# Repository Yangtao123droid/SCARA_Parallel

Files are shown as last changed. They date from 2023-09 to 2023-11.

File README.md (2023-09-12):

【SCARA_Parallel】
=

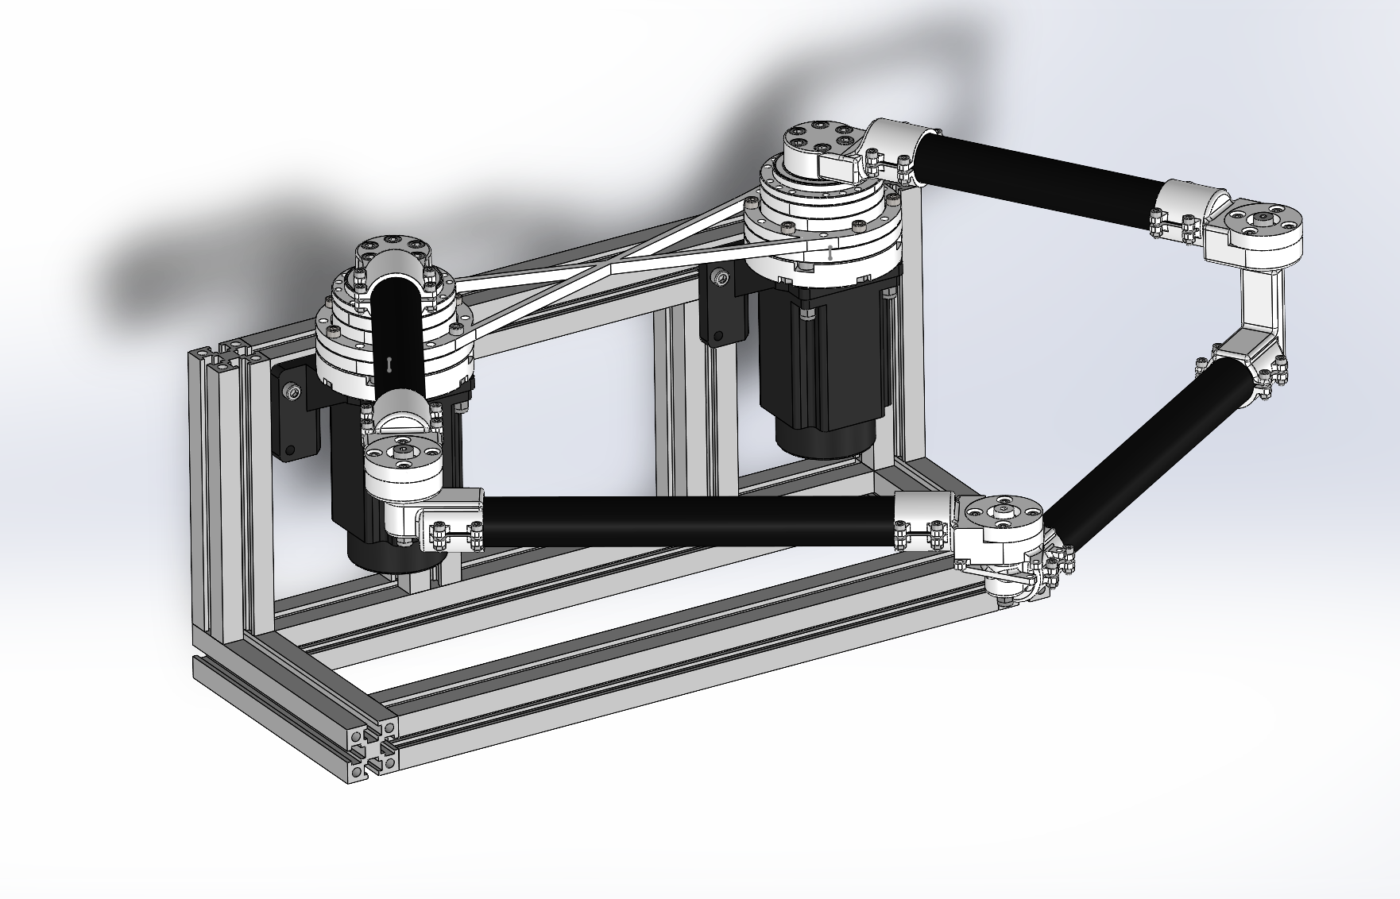
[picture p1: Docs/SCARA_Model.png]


毕设设计的一款并联SCARA机械臂，闭环步进电机，谐波减速，碳纤维杆件，3D打印关节，运动控制，直线插补
=
后面会慢慢更新MATLAB运动学仿真、基于STM32F407的运动控制代码、插补代码以及一些思路分享等等
    
更新说明
=
2023.9.11 更新3D模型 ---所有的零件、电机、减速器、杆件、机加工轴、3D打印关节、装配体文件等等

1、硬件选型与结构设计
=
1.1、电机的选择  
=
电机因为成本考虑问题和项目工作量问题，没有选择使用伺服电机或者无刷电机作为驱动关节，而是选用的
    
闭环步进电机电机的型号是杰美康的57J1880，在闲鱼上淘的,加驱动器一套大概150元，驱动器的型号是2HSS57，

也是杰美康的闭环驱动器，里面自带了电机控制算法，有电流环位置环等等，控制起来和普通的步进电机驱动器  

一样，发脉冲就好了。

后面有时间也许会考虑做一个无刷电机作为关机的版本，FOC控制，可以加入动力学的控制

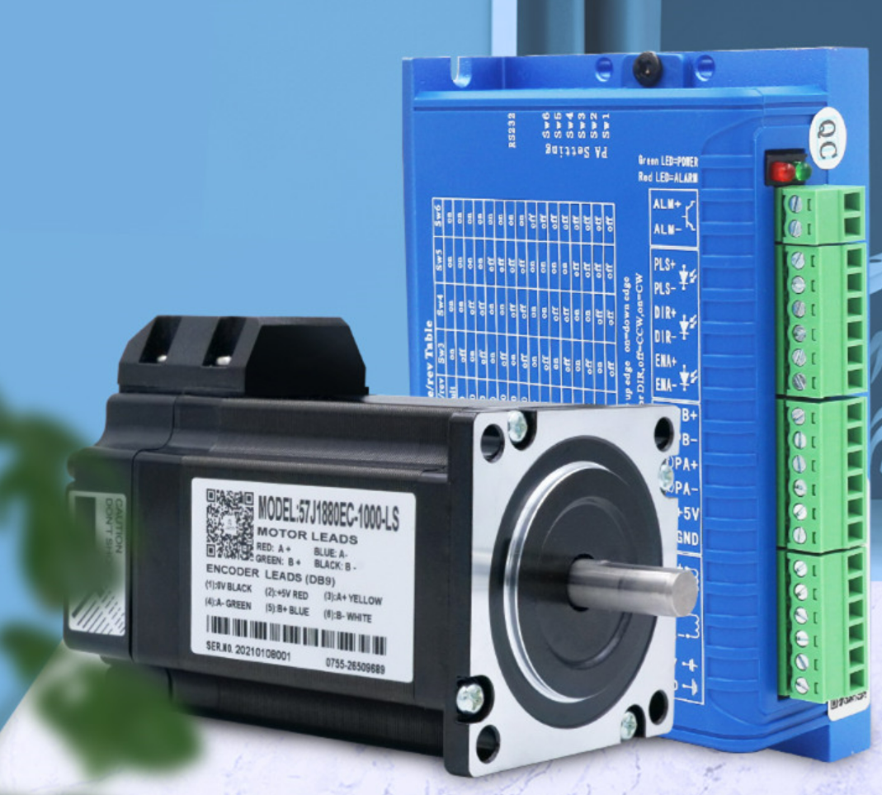
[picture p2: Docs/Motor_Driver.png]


1.2、减速器
=
减速器选用的谐波减速，在闲鱼上淘的leaderdrive绿的谐波的LSCG系列减速器，17-50，减速比50，450元一个，减速器与电机出轴的

尺寸不一样，当时这里自己画了一个连轴器，相当于把电机轴加粗然后插进减速器的孔里面，用键销固定，再上顶丝，电机端

本来就是D型轴，直接卡住就好了，发的模型里面都可以找到零件和装配方法。


1.3、 关节旋转轴
=
这里当时是最苦恼的部分，因为不是机械方面专业的，所以自己完全不知道怎么去设计这部分旋转的关节，后面直接找到了这种

带法兰座的轴承，这样设计起来就容易很多了。
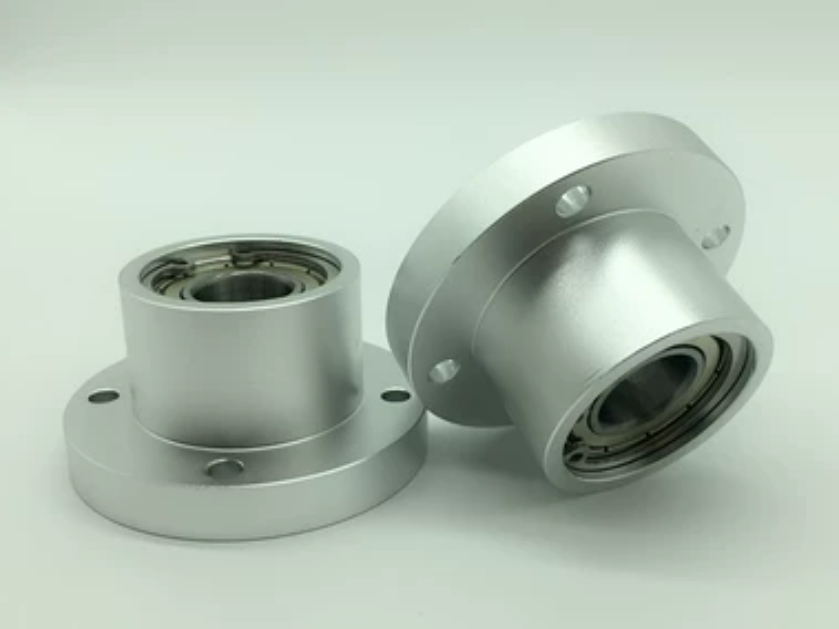
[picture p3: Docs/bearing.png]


1.4、 杆件的选择
=
当时也走了不少弯路，中间有一次甚至直接整个结构都用光固化打印的材料去搭，结果刚度完全不够，搭上去

整个结构就一点一点的塌下去了，后面还是换回了碳纤维管的方案。下面是用过的杆件，整整一箱



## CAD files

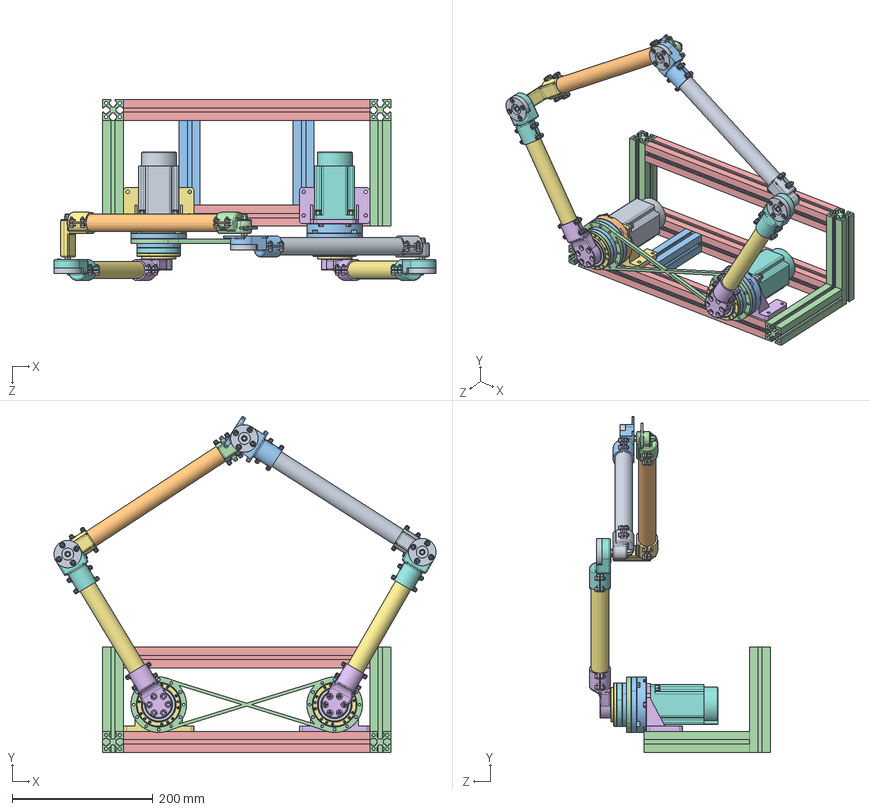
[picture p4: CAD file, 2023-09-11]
Solidworks_Model/SCARA.SLDASM
542.8 x 477.5 x 257.3 mm
闭环步进电机1
闭环步进电机2
电机支架1
电机支架2
减速器固定法兰1
减速器固定法兰2
横350mm x 3
竖150mm x 4
竖120mm x 2
M5锁紧螺母 x 17
RZC-17G______+____^________RZC-17G_LCSG-17-XXX-C-I(2)_LCSG-17-XXX-C-I x 2
RZC-17______^________RZC-17G_LCSG-17-XXX-C-I(2)_LCSG-17-XXX-C-I x 2
LHS-17-XXX-P03-I^LCSG-17-XXX-C-I(2)_LCSG-17-XXX-C-I x 2
DB-17-I^LCSG-17-XXX-C-I(2)_LCSG-17-XXX-C-I x 2
_ISO 7046-1 - M2 x 4 - Z --- 4N^LCSG-17-XXX-C-I(2)_LCSG-17-XXX-C-I x 8
LCS-17-XXX-P01^LCSG-17-XXX-C-I(2)_LCSG-17-XXX-C-I x 2
LCSG-17-P02^LCSG-17-XXX-C-I(2)_LCSG-17-XXX-C-I x 2
LCS-17-P05^LCSG-17-XXX-C-I(2)_LCSG-17-XXX-C-I x 2
________________M5 x 16_________________M5 x 16^LCSG-17-XXX-C-I(2)_LCSG-17-XXX-C-I x 12
LCS-17-P04-3^LCSG-17-XXX-C-I(2)_LCSG-17-XXX-C-I x 2
LCS-17-P04-1^LCSG-17-XXX-C-I(2)_LCSG-17-XXX-C-I x 2
LCS-17-P04-2^LCSG-17-XXX-C-I(2)_LCSG-17-XXX-C-I x 2
15Z-38475^LCSG-17-XXX-C-I(2)_LCSG-17-XXX-C-I x 2
电机轴加粗 x 2
键槽销 x 2
电机距离250mm确认
M4六角螺母 x 12
减速器连接关节 x 2
碳管_185mm x 2
中间关节_上 x 2
轴承 x 3
垫片 x 3
M3X14_固定轴承_中间关节 x 12
M3六角螺母 x 44
M3X12_锁紧碳管 x 32
M5六角螺母 x 3
M5铜柱18mm x 2
中间关节_下_长
M5铜柱50mm
中间关节_下
碳管_270mm
碳管_255mm
末端关节_上
末端关节_下

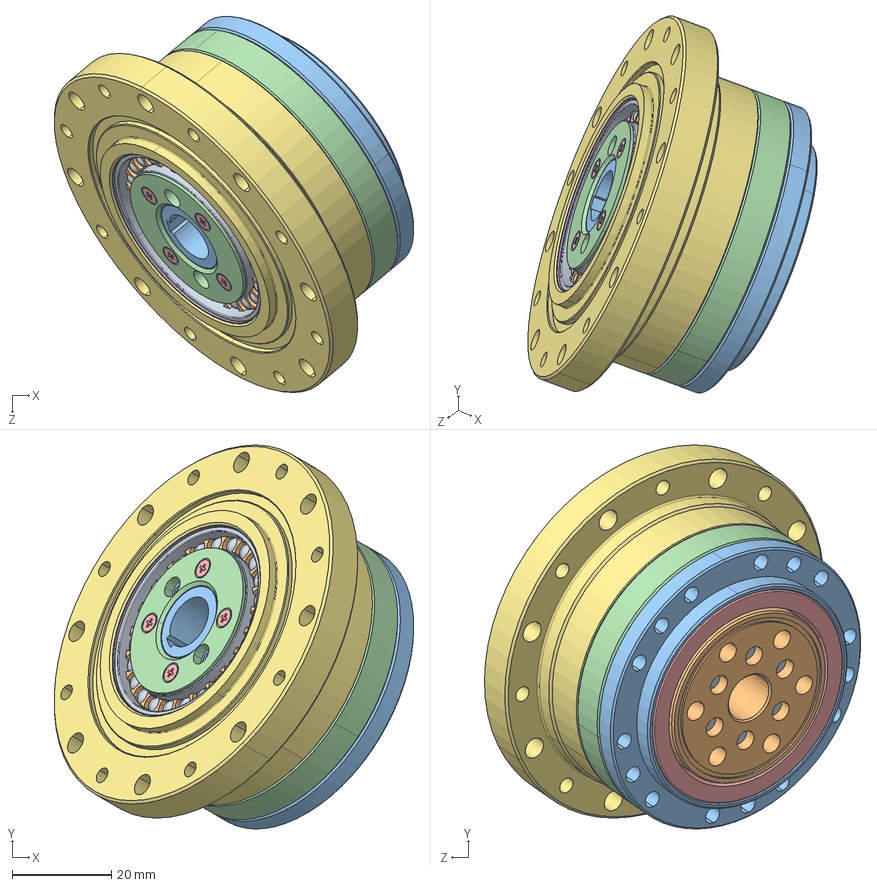
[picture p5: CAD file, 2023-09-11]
Solidworks_Model/减速器/谐波减速.SLDASM
72.3 x 77.3 x 75.7 mm
RZC-17G______+____^________RZC-17G_LCSG-17-XXX-C-I(2)_LCSG-17-XXX-C-I
RZC-17______^________RZC-17G_LCSG-17-XXX-C-I(2)_LCSG-17-XXX-C-I
LHS-17-XXX-P03-I^LCSG-17-XXX-C-I(2)_LCSG-17-XXX-C-I
DB-17-I^LCSG-17-XXX-C-I(2)_LCSG-17-XXX-C-I
_ISO 7046-1 - M2 x 4 - Z --- 4N^LCSG-17-XXX-C-I(2)_LCSG-17-XXX-C-I x 4
LCS-17-XXX-P01^LCSG-17-XXX-C-I(2)_LCSG-17-XXX-C-I
LCSG-17-P02^LCSG-17-XXX-C-I(2)_LCSG-17-XXX-C-I
LCS-17-P05^LCSG-17-XXX-C-I(2)_LCSG-17-XXX-C-I
________________M5 x 16_________________M5 x 16^LCSG-17-XXX-C-I(2)_LCSG-17-XXX-C-I x 6
LCS-17-P04-3^LCSG-17-XXX-C-I(2)_LCSG-17-XXX-C-I
LCS-17-P04-1^LCSG-17-XXX-C-I(2)_LCSG-17-XXX-C-I
LCS-17-P04-2^LCSG-17-XXX-C-I(2)_LCSG-17-XXX-C-I
15Z-38475^LCSG-17-XXX-C-I(2)_LCSG-17-XXX-C-I

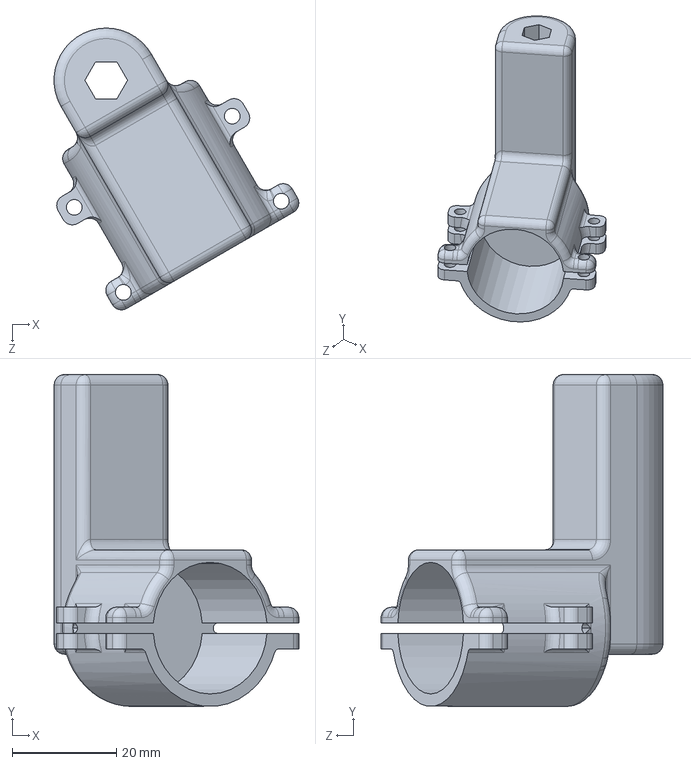
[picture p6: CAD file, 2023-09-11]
Solidworks_Model/打印件/中间关节_下_长.SLDPRT
46.9 x 63.5 x 54.0 mm

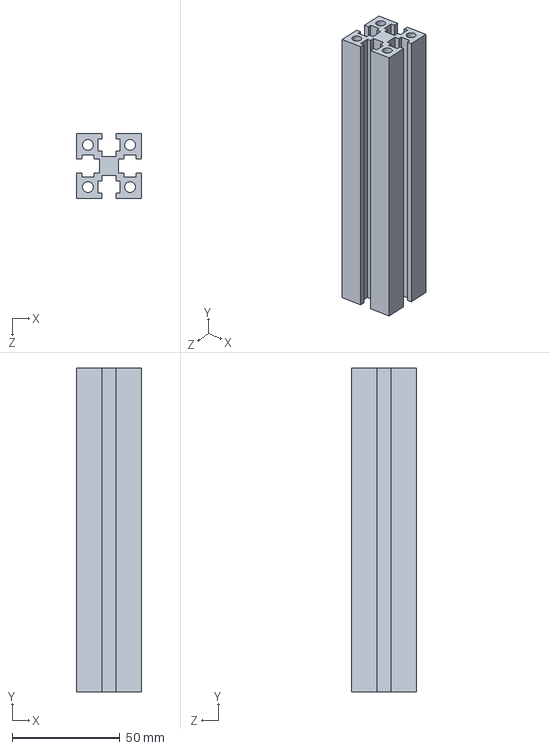
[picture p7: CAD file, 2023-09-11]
Solidworks_Model/机械臂固定底座/竖150mm.SLDPRT
30.0 x 150.0 x 30.0 mm

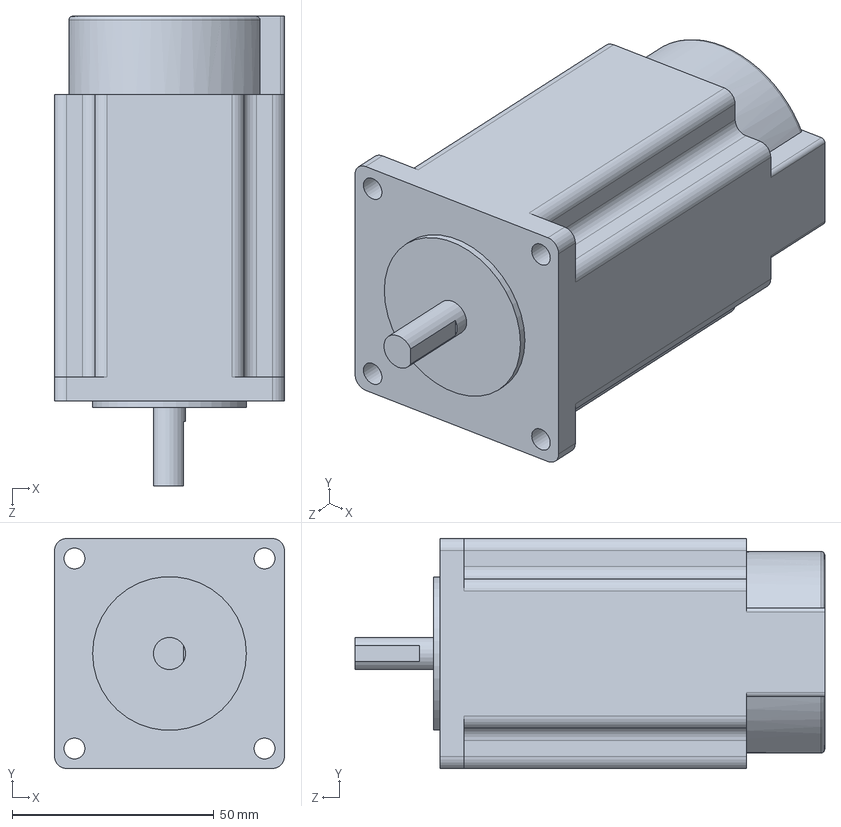
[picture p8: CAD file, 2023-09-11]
Solidworks_Model/电机_支架/闭环步进电机2.SLDPRT
57.0 x 57.0 x 116.4 mm

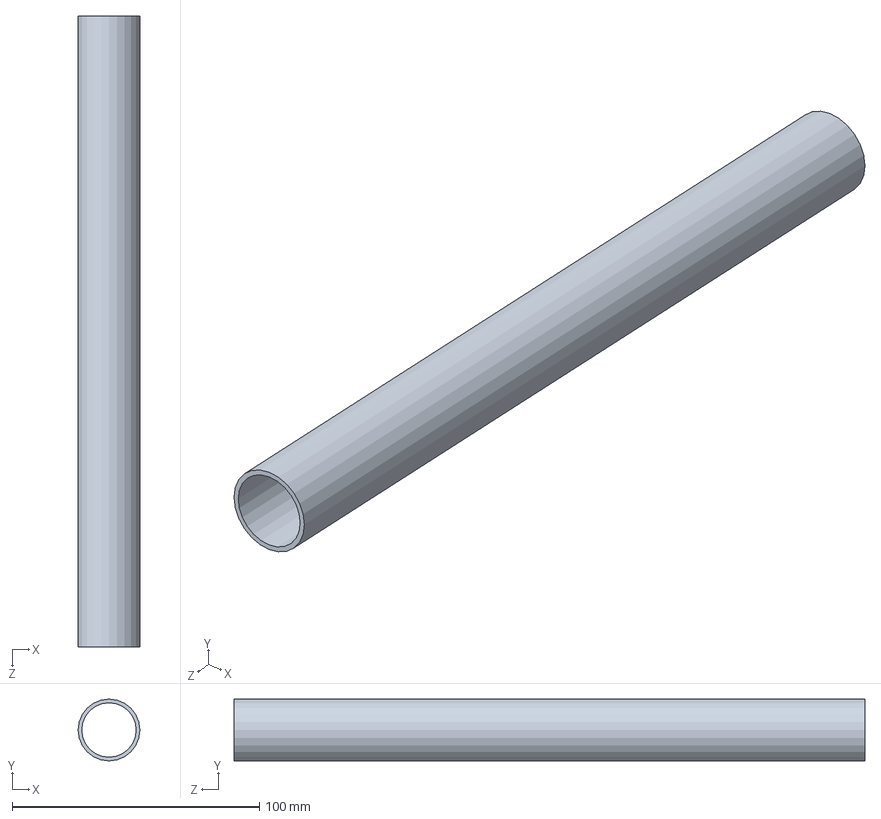
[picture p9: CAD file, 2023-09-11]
Solidworks_Model/碳纤维管/碳管_255mm.SLDPRT
25.0 x 25.0 x 255.0 mm

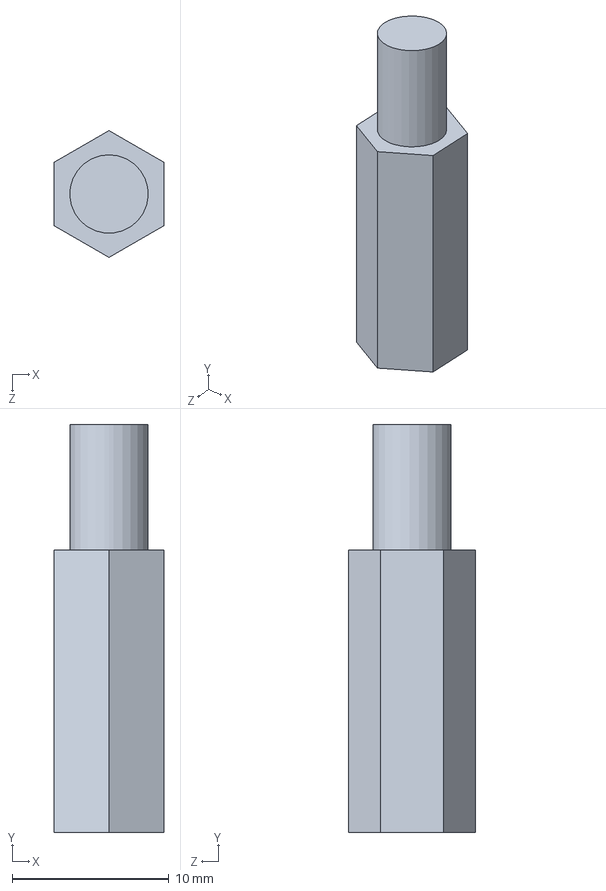
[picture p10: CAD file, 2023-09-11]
Solidworks_Model/螺丝_螺母_垫片_铜柱/M5铜柱18mm.SLDPRT
7.00 x 26.0 x 8.08 mm

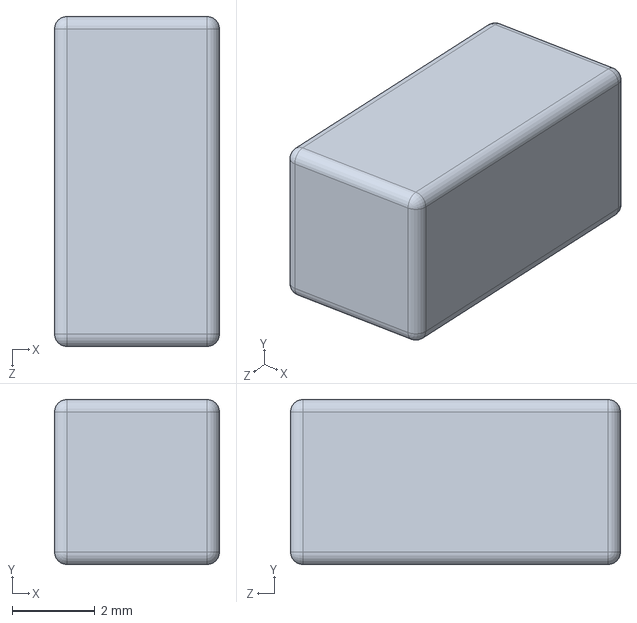
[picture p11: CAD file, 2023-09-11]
Solidworks_Model/轴加工_键槽销/键槽销.SLDPRT
4.00 x 4.00 x 8.00 mm

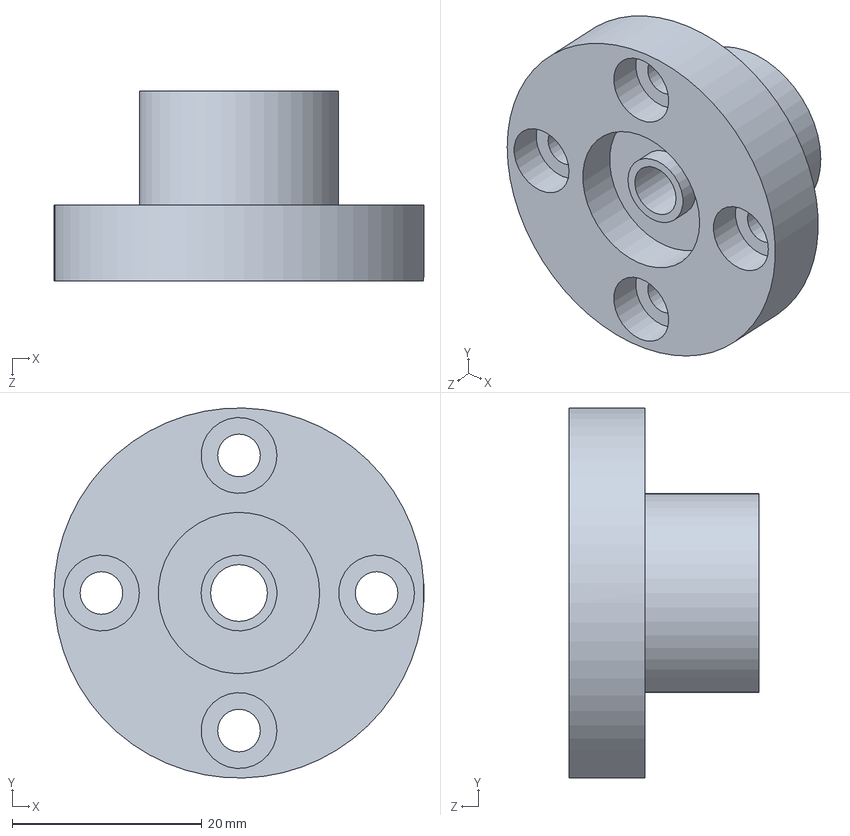
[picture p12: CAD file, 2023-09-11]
Solidworks_Model/轴承/轴承.SLDPRT
39.0 x 39.0 x 20.0 mm

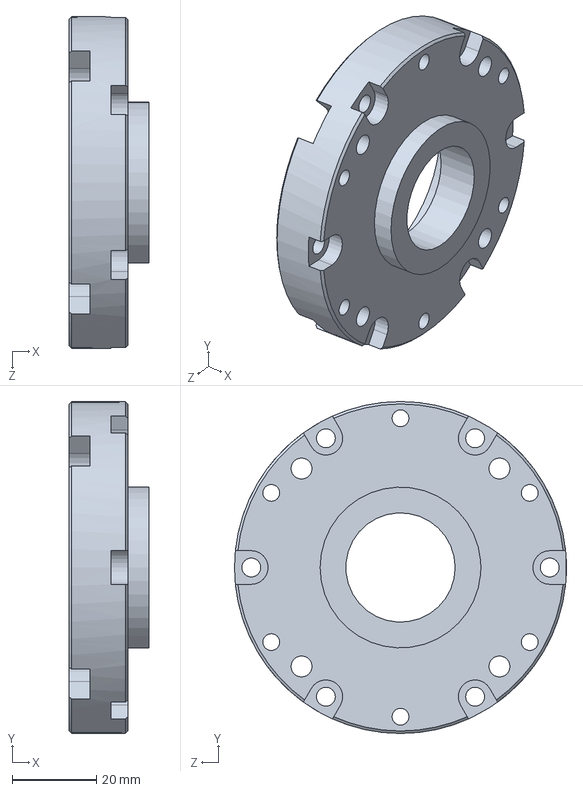
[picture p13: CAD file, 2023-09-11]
Solidworks_Model/打印件/减速器固定法兰2.SLDPRT
19.0 x 79.0 x 79.0 mm

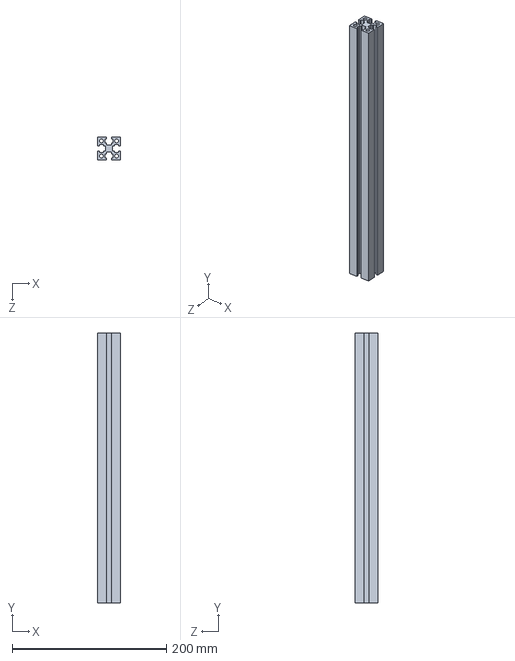
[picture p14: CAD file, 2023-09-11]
Solidworks_Model/机械臂固定底座/横350mm.SLDPRT
30.0 x 350.0 x 30.0 mm

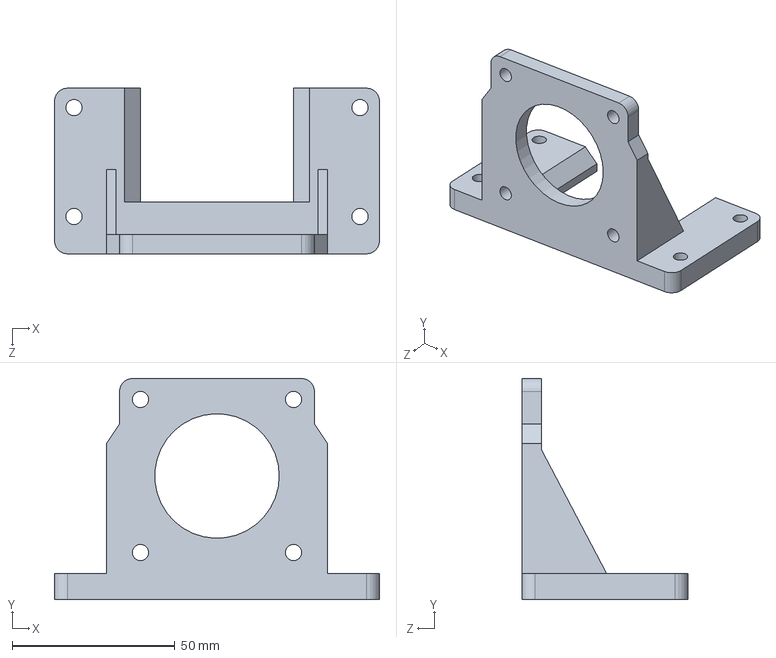
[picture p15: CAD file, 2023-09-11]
Solidworks_Model/电机_支架/电机支架2.SLDPRT
100.0 x 68.0 x 51.0 mm

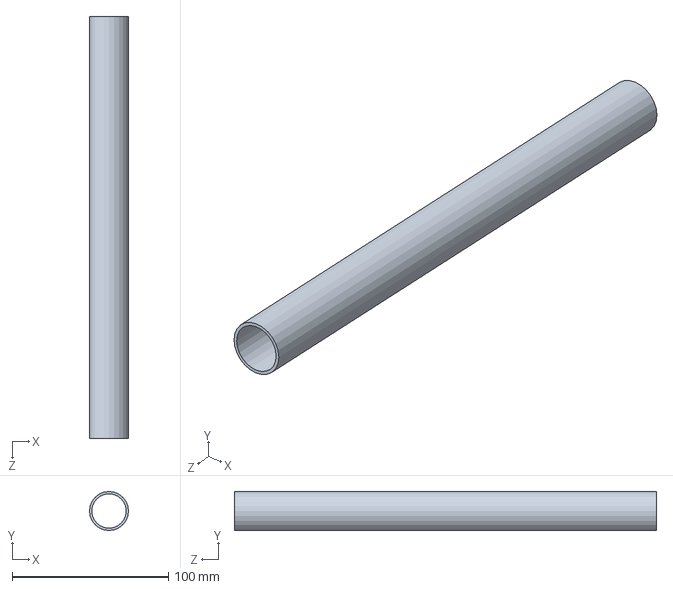
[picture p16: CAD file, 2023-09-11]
Solidworks_Model/碳纤维管/碳管_270mm.SLDPRT
25.0 x 25.0 x 270.0 mm

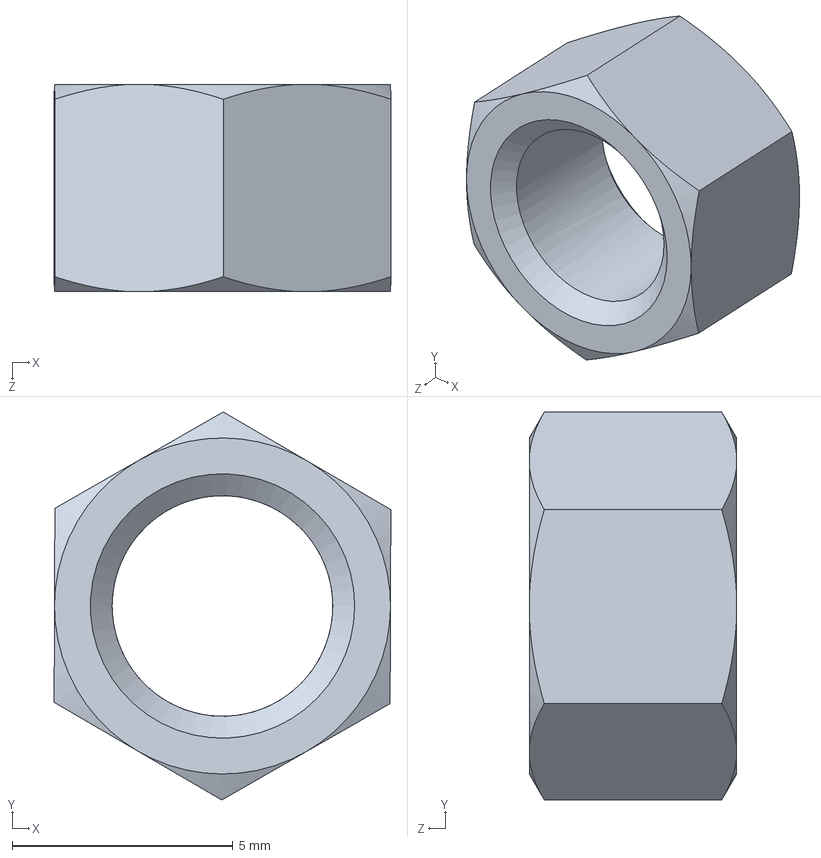
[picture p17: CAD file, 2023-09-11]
Solidworks_Model/螺丝_螺母_垫片_铜柱/M5六角螺母.SLDPRT
7.63 x 8.79 x 4.70 mm

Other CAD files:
Solidworks_Model/轴加工_键槽销/电机轴加粗.SLDPRT
Solidworks_Model/打印件/减速器固定法兰1.SLDPRT
Solidworks_Model/机械臂固定底座/竖120mm.SLDPRT
Solidworks_Model/电机_支架/电机支架1.SLDPRT
Solidworks_Model/打印件/中间关节_上.SLDPRT
Solidworks_Model/打印件/中间关节_下.SLDPRT
Solidworks_Model/打印件/减速器连接关节.SLDPRT
Solidworks_Model/打印件/末端关节_上.SLDPRT
Solidworks_Model/打印件/末端关节_下.SLDPRT
Solidworks_Model/打印件/电机距离250mm确认.SLDPRT
Solidworks_Model/碳纤维管/碳管_185mm.SLDPRT
Solidworks_Model/螺丝_螺母_垫片_铜柱/M3X12_锁紧碳管.SLDPRT
Solidworks_Model/螺丝_螺母_垫片_铜柱/M3X14_固定轴承_中间关节.SLDPRT
Solidworks_Model/螺丝_螺母_垫片_铜柱/M3六角螺母.SLDPRT
Solidworks_Model/螺丝_螺母_垫片_铜柱/M4×25_固定减速器_减速器法兰_电机距离确定打印件.SLDPRT
Solidworks_Model/螺丝_螺母_垫片_铜柱/M4六角螺母.SLDPRT
Solidworks_Model/螺丝_螺母_垫片_铜柱/M5×14_固定电机底座_机械臂底座.SLDPRT
Solidworks_Model/螺丝_螺母_垫片_铜柱/M5×25_固定关节_减速器.SLDPRT
Solidworks_Model/螺丝_螺母_垫片_铜柱/M5×25_固定电机_电机底座_减速器法兰.SLDPRT
Solidworks_Model/螺丝_螺母_垫片_铜柱/M5轴肩螺丝.SLDPRT
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

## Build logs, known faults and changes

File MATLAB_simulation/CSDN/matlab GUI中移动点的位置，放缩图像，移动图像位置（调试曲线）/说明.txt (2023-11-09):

1、进入界面，首先点击初始化按钮，会根据xData和YData数据进行画图（分别是x轴和y轴）

2、启动放缩和关闭放缩可以放缩图像

3、右移和左移图像可以移动坐标轴

4、保存数据按钮可以保存数据，x和y轴数据存在newX和newY数据

5、如果想要移动坐标轴，点击关闭放缩按钮，当鼠标停在数据点上时，按下鼠标左键拖动数据点即可移动数据，（注意，数据点不能是第一个和最后的数据点，且不会超过相邻数据点的范围）

6、另外，xData和yData不用逗号分隔数据，不要修改文件格式

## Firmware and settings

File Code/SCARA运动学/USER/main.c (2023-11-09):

#include "stm32f4xx.h"
#include "delay.h"
#include "led.h"
#include "key.h"
#include "pwm.h"
#include "motor.h" 
#include "SCARA.h"
#include "xbox.h"
#include "openmv.h"
#include "balance.h"

u16 pwmval=0;     
u16 ar1=5000;
u16 ar2=5000;
u16 ar3=5000;
u16 L1=1;
u16 L3=1;
u8 model_S = 0;
u8 key_up1 = 0;
u8 key_up2 = 0;
u8 key_up3 = 0;
u8 key_up4 = 0;
u8 model_pen = 0;

float XNN = 382.3376;


int main(void)
{
	NVIC_PriorityGroupConfig(NVIC_PriorityGroup_2);//设置系统中断优先级分组2
	delay_init(168);
	LED_init();
	KEY_Init();
	MOTOR_Init();
	TIM1_config(ar1-1,21-1);	//84M/84=1Mhz的计数频率,重装载值500，所以PWM频率为 1M/500=2Khz. 
	TIM_SetCompare1(TIM1,ar1/2);	
	TIM8_config(ar2-1,21-1);
	TIM_SetCompare1(TIM8,ar1/2);
	TIM3_config(ar3-1,21-1);
	TIM_SetCompare1(TIM3,ar3/2);
  TIM5_config(50-1,8400-1);	//定时器时钟84M，分频系数8400，所以84M/8400=10Khz的计数频率，计数5000次为500ms     
	uart_init(76800);
	DIR1=1;    //1右
	DIR2=0;    //0左
	
	while(1)
	{
		if(model == 0)
		{
			model=Position_init();
		}
		else
		{
			if(buttonY == 100 && key_up3 == 1) 
			{
				delay_ms(10);             
				key_up3=0;
			if(buttonY == 100)
			{
			  model = 2;
				if(model == 2)
				{
					model = 3;
					arr1 = 500;
					Inverse_motion(125,382.3376);
				}
			}   
		}
		else if(buttonY == 0)
			key_up3 = 1;
		
		if(KEY1 == 1)
		{
			Balance_Begin_flag = 1;
			model = 4;
		}


		
		

//		if((axisY >= 3 || axisX >= 3) && model >= 3 )
//		{
//			model=4;		
//			if(axisY >= 3 && axisX >=3)
//			{
//				LED1=1;
//				if(dirY == 0 && dirX == 0)
//				{
//					X_E=X_N+axisX*0.09;
//					Y_E=Y_N-axisY*0.09;
//				}
//				else if(dirY == 0 && dirX == 1)
//				{
//					X_E=X_N-axisX*0.09;
//					Y_E=Y_N-axisY*0.09;
//				}
//				else if(dirY == 1 && dirX == 0)
//				{
//					X_E=X_N+axisX*0.09;
//					Y_E=Y_N+axisY*0.09;
//				}
//				else if(dirY == 1 && dirX == 1)
//				{
//					X_E=X_N-axisX*0.09;
//					Y_E=Y_N+axisY*0.09;
//				}
//			}
//			else
//			{
//				times=1;
//				model=3;
//		    X_S=X_N;
//		    Y_S=Y_N;
//				X_E=X_N;
//				Y_E=Y_N;
//			}
//		}
		
		if(Y_N >= 450 || Y_N <= 300 || X_N >= 200 || X_N <= 50)
			arr1 = 20000;
		
		
		if(arr1 <= 200)
			arr1 = 200;
		if(arr1 >= 20000)
			arr1 = 20000;
	}
		
//		XNN = 125-(X_N-125);/
//		printf("%.2f\r\n",XNN);//打印
//		printf("%.2f\r\n",Y_N);//打印
	


	  	printf("%.2f\r\n",arr1);//打印

		
//		if(buttonY == 100 && key_up3 == 1) 
//		{
//			delay_ms(10);             
//			key_up3=0;
//			if(buttonY == 100)
//			{
//				 if(model_pen == 0)
//				 {
//					 DIR3=!DIR3;
//					 model_pen=1;
//					 TIM_Cmd(TIM3, ENABLE);  //使能TIM3
//					 delay_ms(300);
//					 TIM_Cmd(TIM3, DISABLE);  //使能TIM3
//					 model_pen=0;
//				 }
//				 LED1=1;
//			}   
//		}
//		else if(buttonY == 0)
//			key_up3 = 1;
	}
}

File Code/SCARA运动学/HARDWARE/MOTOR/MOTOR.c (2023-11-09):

#include "motor.h" 
//////////////////////////////////////////////////////////////////////////////////	 
 
//LED驱动代码	   
//STM32F4工程-库函数版本
//淘宝店铺：http://mcudev.taobao.com									  
////////////////////////////////////////////////////////////////////////////////// 	 

//初始化PF9和PF10为输出口.并使能这两个口的时钟		    
//LED IO初始化
void MOTOR_Init(void)
{    	 
  GPIO_InitTypeDef  GPIO_InitStructure;

	RCC_AHB1PeriphClockCmd(RCC_AHB1Periph_GPIOA, ENABLE);//使能GPIOF时钟

	
  GPIO_InitStructure.GPIO_Pin = GPIO_Pin_2 | GPIO_Pin_1 | GPIO_Pin_3 | GPIO_Pin_4 | GPIO_Pin_7;
  GPIO_InitStructure.GPIO_Mode = GPIO_Mode_OUT;//普通输出模式
  GPIO_InitStructure.GPIO_OType = GPIO_OType_PP;//推挽输出
  GPIO_InitStructure.GPIO_Speed = GPIO_Speed_100MHz;//100MHz
  GPIO_InitStructure.GPIO_PuPd = GPIO_PuPd_UP;//上拉
  GPIO_Init(GPIOA, &GPIO_InitStructure);//初始化
	
	GPIO_SetBits(GPIOA,GPIO_Pin_2 | GPIO_Pin_1 | GPIO_Pin_3 | GPIO_Pin_4 | GPIO_Pin_7);

}

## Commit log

2023-09-11 上传3D模型
    [M3X12_锁紧碳管.SLDPRT, M3X14_固定轴承_中间关节.SLDPRT, M3六角螺母.SLDPRT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]
2023-09-12 提交照片
2023-09-12 提交图片
2023-11-09 上传MATLAB仿真以及STM32代码
